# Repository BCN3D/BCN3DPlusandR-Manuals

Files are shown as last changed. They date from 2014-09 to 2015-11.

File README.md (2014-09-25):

BCN3D+ Manuals
==============

Close up view of the printer

We've made some pretty awesome manuals to help you assembling the BCN3D+. We have two versions, the **PDF** and the **3DVIA**. All the manuals are based on the 3D model of the printer, so you'll be able to see 3D assemblies with all the parts and pieces.

Again, the manuals are supposed to guide you in the process of assembling the printer. If you detect any mistake or improvement, please let us know by submitting and Issue in the git repo.

The good stuff comes when you use the 3DVIA manuals. An executable application lets you rotate, zoom and select the parts in a 3D dimensional way. Easy as pie!

3DVIA visualization example

You can find the following assembly manuals:

+ BCN3D+ 3D printer
+ BCNozzle, the full metal hot-end upgrade for multiple 3D printers
+ Dual Extruder, all the steps to assembly the dual extruder upgrade

*New and updated Manuals are coming... just follow us on Github to be up to date!*

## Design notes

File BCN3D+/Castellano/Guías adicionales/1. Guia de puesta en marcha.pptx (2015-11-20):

## Puesta en marcha Encendido y ajustes previos al funcionamiento de la máquina

Equipo RepRapBCN

## Puesta en marcha

- Con el conexionado listo y el firmware ya instalado se puede arrancar la máquina. Para hacerlo sólo hay que apretar el interruptor de la parte posterior.
- La pantalla debería quedar como en la imagen:
- Cuando se haga por primera vez es importante estar atentos a posibles ruidos o cualquier anomalía.
NOTA:

Si ha recibido su maquina ya montada no es imprescindible que realice muchas de las siguientes comprobaciones aunque es recomendable hacerlas para detectar posibles problemas y para familiarizarse con su funcionamiento.

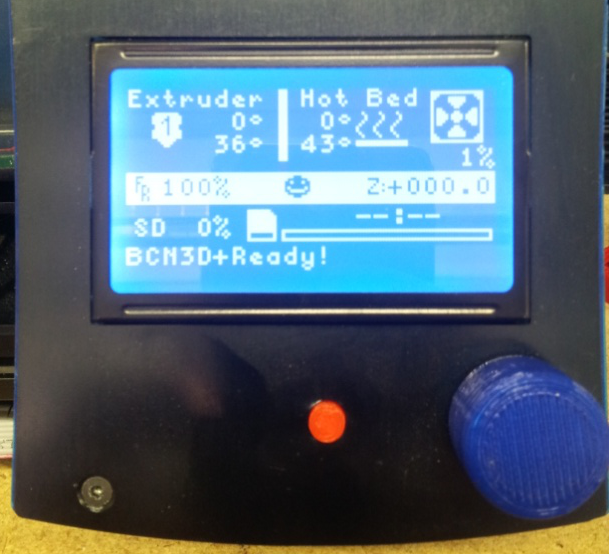
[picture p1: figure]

Dudas?

## Puesta en marcha

Árbol de menús de la pantalla

- Para entrar en el árbol pulse el botón giratorio:
- Prepare
  - Dissable steppers (desbloquea motores para movimiento manual)
  - AutoHome (Lleva la máquina a x=0, y=0, z=0)
  - Preheat (Precalentamiento de máquina)
  - Cooldown (Enfriamiento de máquina)
  - Move Axis (Movimiento de ejes desde pantalla)
- Control
  - Temperature
    - Nozzle (elección manual de temperatura del extrusor)
    - Bed (elección manual de la temperatura de la base calefactora)
  - Motion

Para saber mas sobre el resto de opciones del menú visitad y comentad nuestro foro. (http://www.reprapbcn.com/es/forum)

Dudas?

## Puesta en marcha

- Comprobaciones de funcionamiento: Termistores y motores X e Y

- Termistores:
  - Verificar que la temperatura que miden es “lógica”. La pantalla debería mostrar temperaturas que ronden la temperatura del ambiente.
- ~025/000°
- Orientación de motores X e Y:
  - Entrar en el menú: Prepare > Move Axis
  - Seleccionar 1mm y seleccionar X. Al girar la rueda en sentido horario el carro con el extrusor debería moverse hacia la derecha (acercarse al final de carrera).
  - Si no lo hace, apagar la máquina y cambiar orientación del conector del motor X en la placa.
  - Hacer esta misma comprobación para el eje Y. (en este caso debe alejarse del final de carrera Y)

Dudas?

## Puesta en marcha

- Comprobaciones de funcionamiento : Motor Z

- Orientación del motor Z:
  - Seleccionar Z en el menú Move Axis
  - Girar la rueda MUY POCO en sentido horario
  - Comprobar que los dos motores giran en el mismo sentido.
  - Si no es así parar máquina y girar una de las dos conexiones. (Ambos motores deberán seguir el mismo código de colores)
  - Volver a mover el eje. Ahora se puede girar la rueda sin miedo.
  - Comprobar que el eje Z está subiendo al girar la rueda en sentido horario.
  - Si no lo hace girar los dos conectores

Dudas?

## Puesta en marcha

- Sistema de ejes

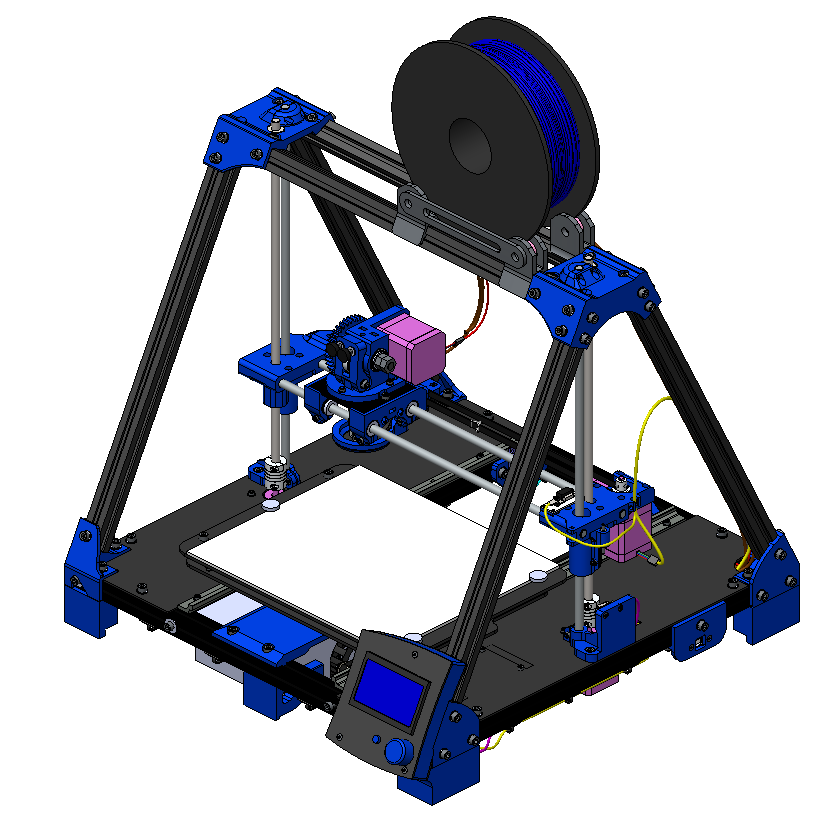
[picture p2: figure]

EJE X

EJE Y

EJE Z

EJE E

Dudas?

## Puesta en marcha

Comprobaciones de funcionamiento: Finales de carrera

- Localizar todos los finales de carrera (X, Y y Z en este orden)
- Comprobar que los finales de carrera contactan correctamente con la parte móvil correspondiente de cada eje en cuanto ésta se acerque a ellos y que el LED se enciende cuando los pulsa.
- Si al pulsar un final de carrera se corta la alimentación de la máquina es probable que alguno de los extremos del final de carrera esté conectado en sentido incorrecto.

Para el eje Z realizar estas comprobaciones con el prisionero de regulación en la posición más alta (que el tornillo salga lo máximo por debajo de la pieza) para evitar contacto entre extrusor y base.

Dudas?

## Puesta en marcha

A continuación se va a comprobar el funcionamiento de los finales de carrera manualmente:
  - Acceder al menú prepare y colocar el cursor en la opción Autohome SIN PULSARLA
  - En el momento en que se active el Autohome el eje X irá hacia el final de carrera, luego lo hará el Y, y luego el Z.
  - A medida que los ejes se muevan, pulsar con la mano el final de carrera correspondiente. Si al pulsar alguno de los finales de carrera no se detiene el movimiento del eje, parar máquina de inmediato.
  - Si se produce este error querrá decir que, aunque están bien conectados, las posiciones de los finales de carrera en la placa están intercambiadas. Comprobarlo y conectarlo correctamente.
  - Cuando la prueba anterior se realice correctamente, pulsar Autohome otra vez para verificar el contacto de la pieza móvil con el final de carrera.

El objetivo es activar los finales de carrera con el dedo antes de que lo hagan las partes móviles de la máquina

Dudas?

## Puesta en marcha

- Comprobaciones de funcionamiento: Resistencias y calentamiento

- Activación del calentamiento:
- Seleccionar en el menú prepare > Preheat PLA.
- Al escoger esta opción se empezará a calentar la base y el extrusor hasta las temperaturas establecidas en el firmware.
- Comprobar que en la pantalla principal aparecen temperaturas objetivo: Extrusor y Base calefactada.
- Dejar calentar y ver si se llega a la temperatura objetivo. (El extrusor debe tardar menos de 5 min, mientras que la base puede llegar a tardar 15 min).

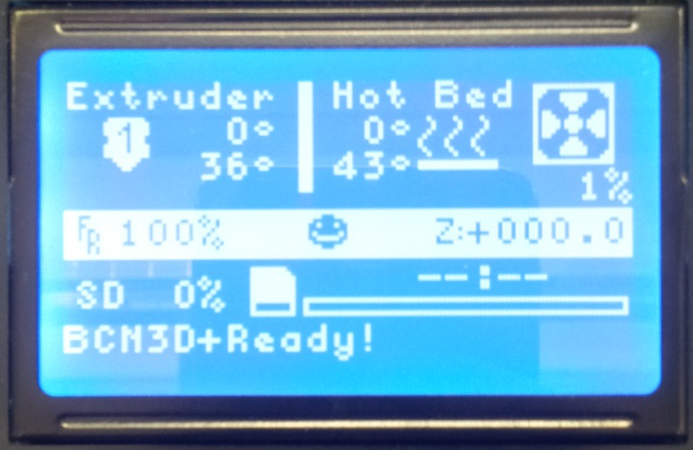
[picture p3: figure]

Dudas?

## Puesta en marcha

Comprobaciones de funcionamiento: Extrusor

- Una vez el extrusor esté a la temperatura preestablecida para el PLA, pulsar 1mm > Extruder en el menú de Move Axis y comprobar que el engranaje grande gira en el sentido de las agujas del reloj.
- Si no es así, cambiar la orientación del conector del motor en la placa electrónica.

Esta comprobación se deber realizar con la máquina caliente y el extrusor a la temperatura del hilo que se va a extruir (PLA ± 190/220ºC , ABS ± 230/250ºC)
Para modificar las temperaturas objetivo seleccionar Temperature >Nozzle en el menú Control

Dudas?

## Puesta en marcha

Comprobaciones de funcionamiento: Extrusor

- Cuando el sentido de giro ya sea el correcto, comprobar que el ventilador del disipador (el mas pequeño esté funcionando)
- Abrir el fijador del extrusor y pasar hilo por el agujero. Asegurarse que el hilo encara el segundo agujero
- Introduciendo hilo con suavidad hasta que éste empieza a salir fundido por la boquilla.
- Cerrar el fijador de manera que ejerza una cierta presión.
  - Demasiada fuerza erosionará el hilo y no traccionará correctamente con la parte grafilada
  - Poca fuerza dejará el hilo suelto y tampoco saldrá.

Esta comprobación se deber realizar con la máquina caliente y el extrusor a la temperatura del hilo que se va a extruir (PLA ± 190/220ºC , ABS ± 230/250ºC)
Para modificar las temperaturas objetivo seleccionar Temperature >Nozzle en el menú Control

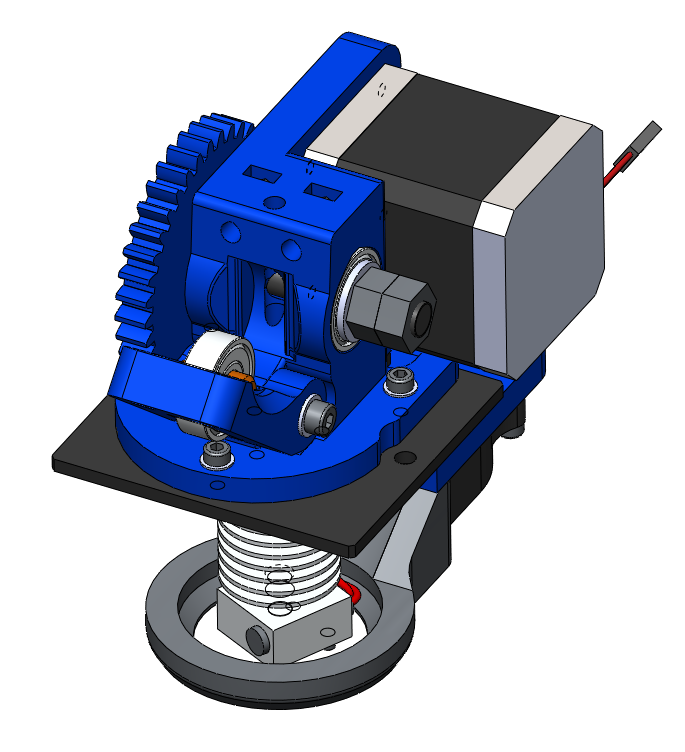
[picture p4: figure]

Dudas?

## Puesta en marcha

Comprobaciones de funcionamiento: Extrusor

- Una vez preparado el hilo se accede al menu prepare > move axis > 1mm > Extruder SIN apretarlo.
- Colocar los dedos en la parte del hilo que justo entra por el orificio superior y le damos a Extrude
- Comprobar si el extrusor tira el hilo (dejando que este entre. NUNCA intentando evitar el movimiento del hilo)
- Pulsar varias veces a Extrude hasta que el plástico salga de manera fluida y continua por la boquilla.

Vigilar no poner los dedos en contacto con ninguna parte móvil que no sea el hilo!

Dudas?

## Esperamos que hayais disfrutado de la experiencia! No olvidéis seguirnos en Twitter y Facebook Para cualquier duda visita nuestro foro (http://www.reprapbcn.com/es/forum)!

- Equipo RepRapBCN

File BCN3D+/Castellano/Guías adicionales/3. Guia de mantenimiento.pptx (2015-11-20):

## Recomendaciones de uso y mantenimiento Algunos consejos para que pueda sacar el máximo partido a su impresora y asegurar su buen funcionamiento

Equipo RepRapBCN

## Recomendaciones de uso y mantenimiento

- Ajustes del eje Z

- A pesar de tener la máquina calibrada, es posible que al empezar a imprimir la pieza, la boquilla quede demasiado alta. Esto se identifica porqué en vez de dejar un hilo constante, va soltando gotitas de material fundido.
- Se puede solucionar provisionalmente este problema girando a mano las dos varillas del eje Z en sentido antihorario. Hay que vigilar de girar el mismo número de pasos las dos varillas para no descalibrar la máquina.

Las gotitas también se producen cuando el extrusor aun no ha llegado a estabilizarse en fundir plástico. Esperar unas cuantas pasadas antes de diagnosticar el problema.

Tener mucho cuidado, ya que son elementos móviles accionados por el motor!

Dudas?

## Recomendaciones de uso y mantenimiento

- Extracción de piezas

- Para retirar las piezas de la base, retirar primero el vidrio quitando al menos uno de los tornillos blancos (de poliamida) que lo sujetan.
- Una vez extraído de la máquina, separar las piezas de la base. De esta manera se reduce considerablemente el riesgo de descalibrado de la máquina.
- Cada cierto número de impresiones es recomendable limpiar la base.

Dudas?

## Recomendaciones de uso y mantenimiento

- Adherencia de la superficie caliente

- Para mejorar la adherencia de las piezas a la base calefactada es bueno usar laca (suministrada en el kit) especialmente para el ABS.
- Para aplicar la laca sobre el vidrio vaporizarla a una distancia entre 30 y 40 cm. Sobre toda la superficie del vidrio.

Dudas?

## Recomendaciones de uso y mantenimiento

Limpieza del extrusor

- Cada cierto tiempo de uso, es recomendable limpiar el exterior de la boquilla del extrusor.
- Se puede hacer dando varias pasadas por la boquilla (con el extrusor caliente) con un paño mojado en acetona (o producto similar).

El contacto con el extrusor puede producir quemaduras graves. Tener mucho cuidado al realizar este paso. Igualmente, no mantener el contacto entre el paño y la boquilla muchos segundos, ya que se puede quemar paño.

Dudas?

## Recomendaciones de uso y mantenimiento

- ¿Cuándo calibrar?

- Cuando se aprecie una diferencia de altura de la primera capa al empezar una impresión.
- Cada cierto tiempo y según el gusto personal.
- Lo importante es que la máquina imprima la primera capa bien, con el material bien pegado a la superficie.

Dudas?

## Esperamos que hayais disfrutado de la experiencia! No olvidéis seguirnos en Twitter y Facebook Para cualquier duda visita nuestro foro (http://www.reprapbcn.com/es/forum)!

- Equipo RepRapBCN

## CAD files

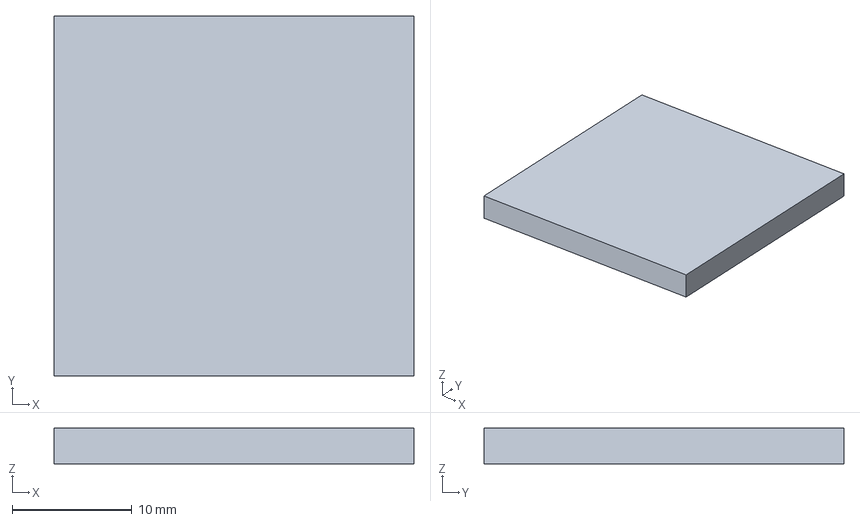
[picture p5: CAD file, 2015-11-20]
Dual Extruder/Calibration, set up/Calib.amf
30.0 x 30.0 x 3.00 mm

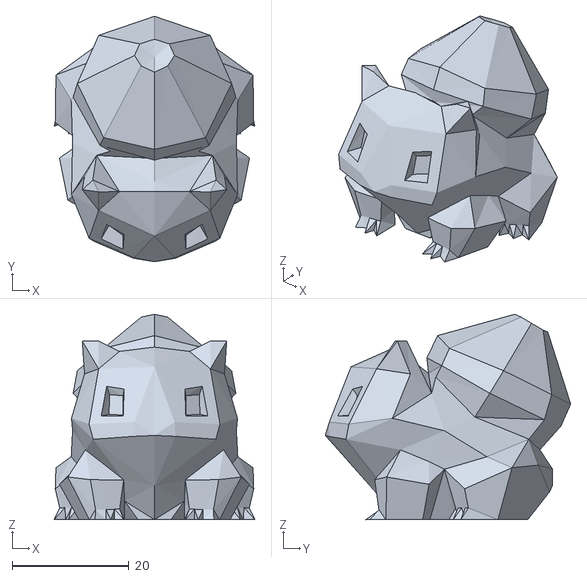
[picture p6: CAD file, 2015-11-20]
Paste extruder/Files for the set up, first run/STLs/bulbasaur.STL
34.4 x 42.0 x 35.2

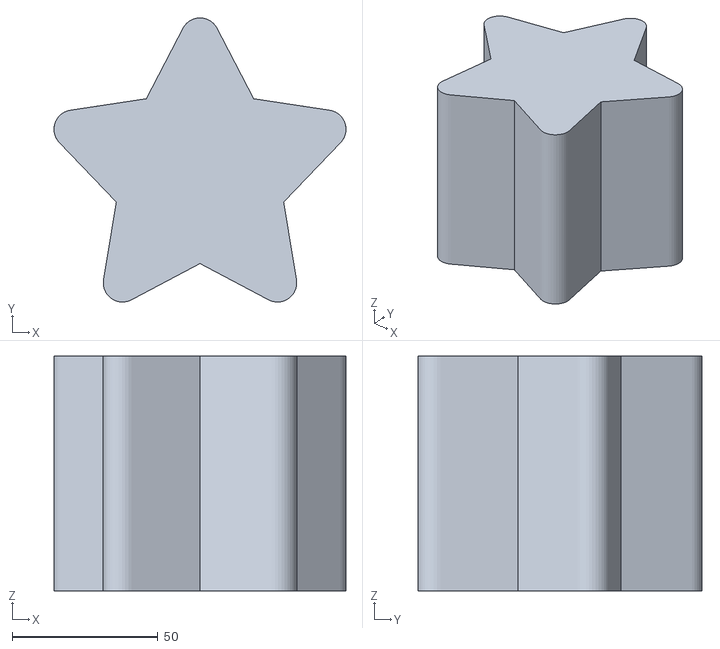
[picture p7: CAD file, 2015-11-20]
Paste extruder/Files for the set up, first run/STLs/star.stl
100.3 x 97.6 x 80.5

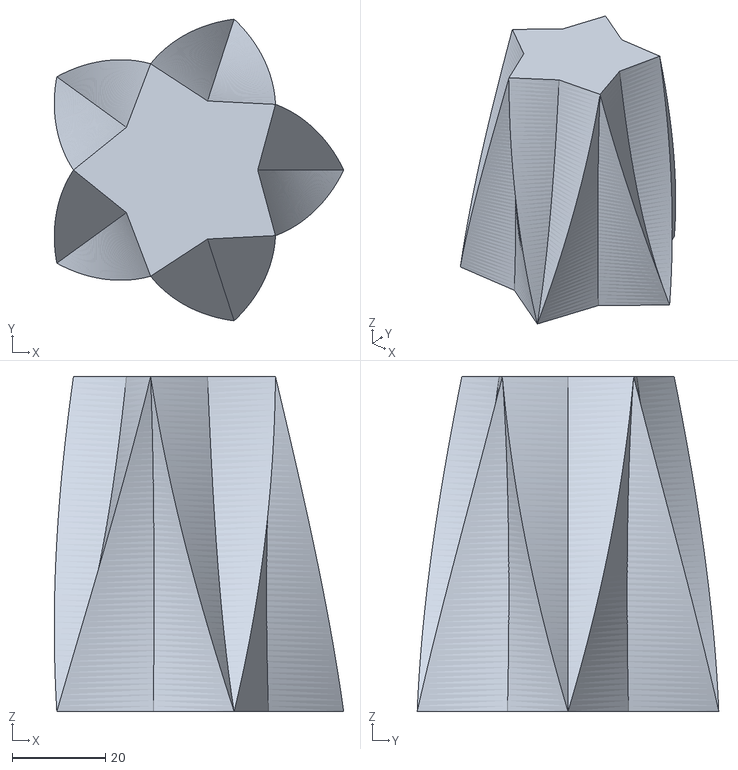
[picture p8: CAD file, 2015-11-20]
Paste extruder/Files for the set up, first run/STLs/star-vase.stl
62.2 x 64.8 x 72.0

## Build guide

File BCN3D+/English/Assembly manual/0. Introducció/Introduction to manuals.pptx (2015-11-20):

## Introduction to manuals Information for the proper use of the manuals

- RepRapBCN Team

## Welcome

- If you're holding this book means you're ready to start assembling your BCN3D+ . We hope you will enjoy the experience during the construction process of your printer and also after creating your pieces.
- Before you start we going to make a brief introduction to the series of manuals for a even easier experience.

## Location of the manuals

- In the directory of manuals from the SD card are 8 folders. Each corresponds to a subsystem of the printer and will assemble them in the indicated order.
- This way we begin with the structure of the printer, to continue with the elements that allow movement in all three axes (Y, X and Z). With all the mechanics prepared just miss to add the electronics and LCD screen, and finally the wiring.

## File types

- In each folder you will find 2 types of file with the same name:
  - *.exe file is an application that offers an interactive guide assembly. You can zoom, move and rotate the view. We recommend this to use because it allows much better understanding of the assembly.
  - *.pdf file is a sequence of images that correspond to the interactive slides manual. It's equivalent to the above but designed for those users who can not run the application (especially Mac and Linux). Also useful is the .pdf file if you want to assemble the printer with a paper edition of the manual.

## Interactive operation manual

- The application of the interactive manual is easy to use, you just need to know the icons to manipulate the views of the 3D printer assembly :

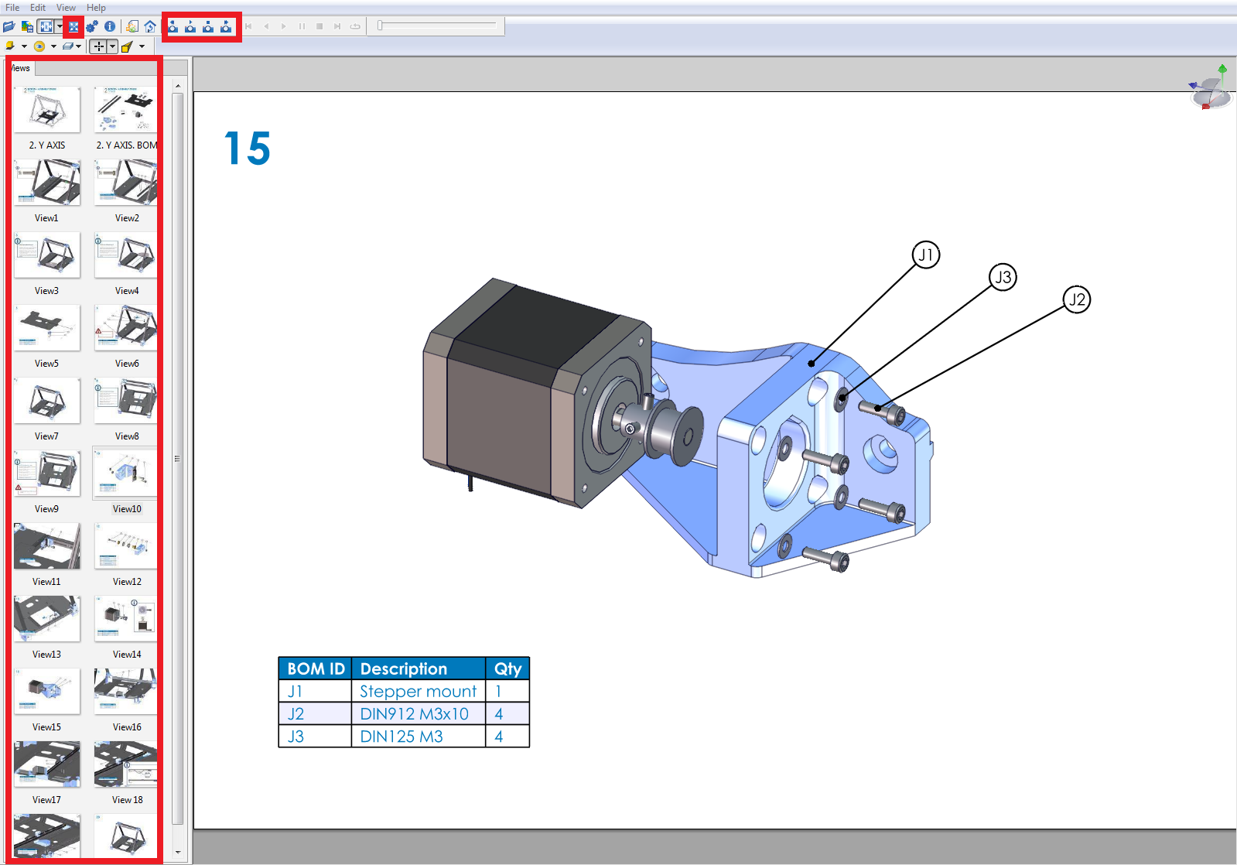
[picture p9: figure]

## Interactive operation manual: Navigation

  - Sequential Navigation: To get around the manual you can use the buttons on the top. With them you can go back to a slide, play in auto mode, stop the auto play and go to a slide, in the order they appear.
          - Sequential Navigation: To get around the manual you can use the buttons on the top. With them you can go back to a slide, advance in auto mode, stop the auto play and go to a slide, in the order they appear.

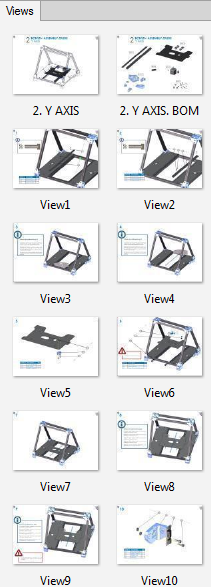
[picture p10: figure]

## Interactive operation manual: Navigation

- Zoom in / out: By rotating the mouse wheel you can change the zoom and focus on the area you want.
- Move: With the same wheel, but using it in button mode you can scroll the image. This way you can move to different parts of the printer without changing the perspective.
- Rotate: If you need to get another point of view, you can change the perspective by using the right mouse button, holding it down while you rotate the view.

## Structure of the chapters

1st Page: Presentation of Chapter
The title of the chapter and the whole machine is displayed on the first slide, with the silhouette of the pieces you have assembled so far and in color which have to be installed in this chapter.

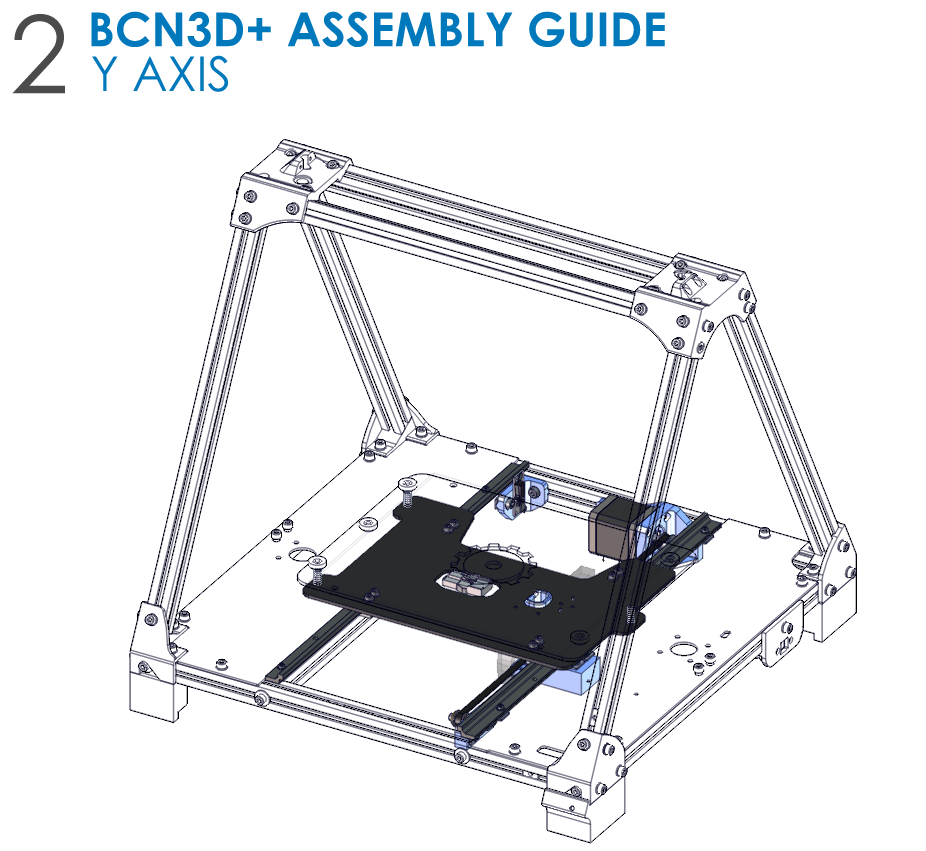
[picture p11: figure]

## Structure of the chapters

2nd page: parts distribution in boxes
The second page is a summary of the parts to be used in this chapter, grouped by type of part, to identify where you have to look for each one.
It is important to remember that NOT all parts are listed only the main ones, is just to know in which boxes are the necessary equipment.

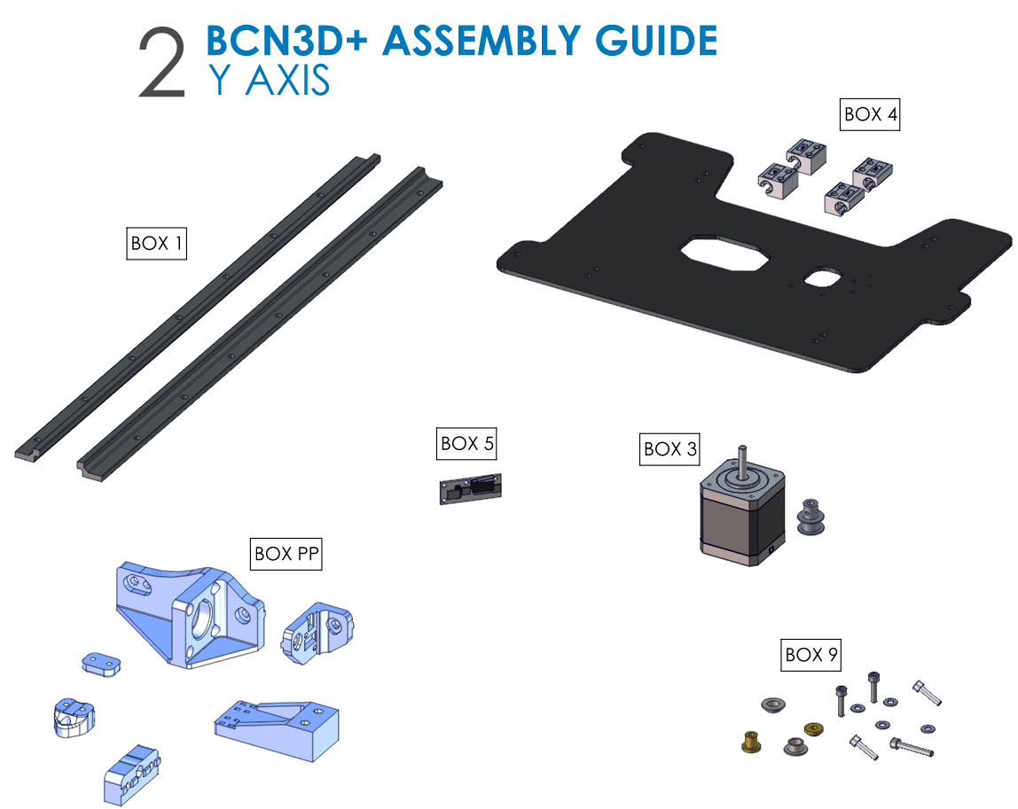
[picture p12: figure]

## Structure of the chapters

Other pages: Installation steps
Each of the steps shown in a slide type that has common elements: slide number, steps to follow, list of components, callouts and annotations component ID number (only when necessary).

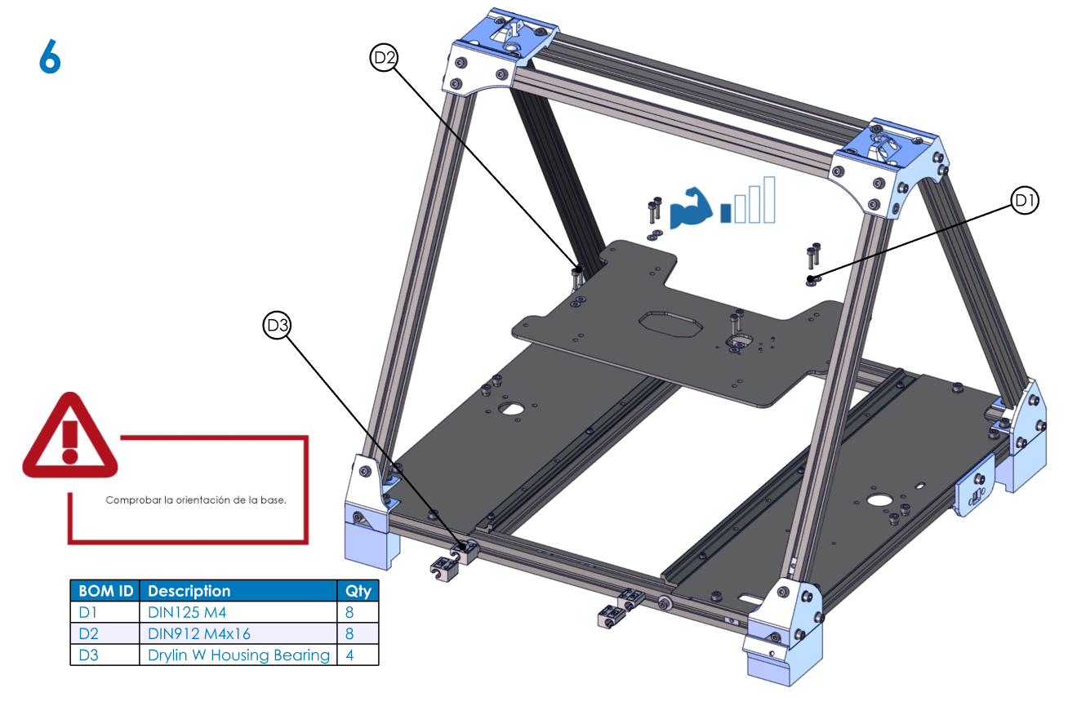
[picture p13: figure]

## Structure of the chapters

- Common elements
- Slide Number: Located in the top left, and helps identify the step that is being processing.
- Steps to perform: Figure of the machine tells you the components to be mounted on that step. When you change the slide, the components are moved to the mounting position. Back and forth you can get a better idea of how to mount the component, and you can repeat this step as many times as you needed.

## Structure of the chapters

- Common elements
- List of components: The table is usually found on the bottom left (although sometimes may appear elsewhere) indicates the components that you need in that step. The first column is the ID part of the manual, the second is the name and the third the quantity. We recommend to prepare all the parts of the table before you start assembling the step.
- The callouts component indicator: Indicator used to easily identify the parts to be assembled in 3D view. The callouts still appears even rotate the 3D view and if necessary, you can move to have a clearer view and to avoid crossing the image. Just click on the callouts itself and without releasing the mouse button, drag it to the desired position.

## Structure of the chapters

- Notes: In the slides that require it, a series of annotations. Each symbol corresponds to the message that is described below:

INFORMATION: Always accompanied by an explanatory note that is not essential for the assembly of the printer but is useful to facilitate understanding of the manual.

CAUTION: This icon is always accompanied by an essential explanatory annotation for the correct assembly of the printer.

NOT: Indicates something that should not be as in the picture. It also used to help distinguish between components to be used.

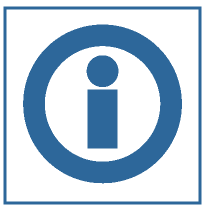
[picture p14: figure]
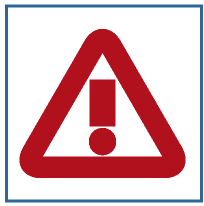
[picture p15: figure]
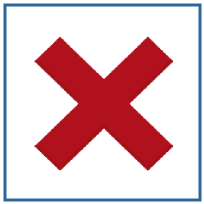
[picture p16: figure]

## Structure of the chapters

TIGHTEN WITH FINGER: Indicates something that should hold it by hand until it locks in a definitive way.

THREAD: Indicates the component that affects must be threaded.

FLAT SURFACE: Indicates that the operation referred to must be performed on a flat surface. Affects critical parts of the structure and serves to ensure a good reference planes for other mechanisms.

FLANGE CLOSE: This icon indicates that the corresponding step needs to close one or more flanges at the indicated position.

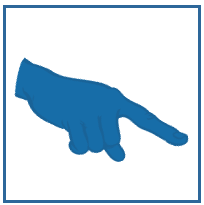
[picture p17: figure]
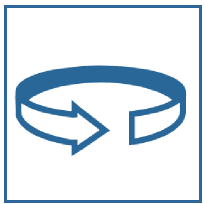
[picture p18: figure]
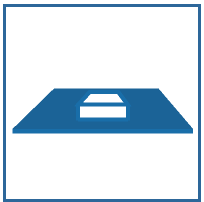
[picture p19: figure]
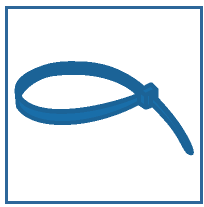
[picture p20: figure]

## Structure of the chapters

SOFT TIGHTEN: Indicates that this torque should be smooth, simply to ensure that the screw is attached to the component without deforming. It usually affects plastic components that can break under excessive force.

TIGHTEN STRONG: Indicates that this torque must be strong to ensure that the component is properly fixed. It usually affects metallic components that transmit important efforts under operation.

FLAT SURFACE: Indicates that the operation referred to must be performed on a flat surface. Affects critical parts of the structure and serves to ensure a good reference planes for the mechanisms.

TAPE: Indicates to use adhesive (or similar) tape during the step to temporarily hold some component.

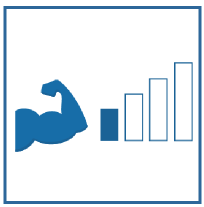
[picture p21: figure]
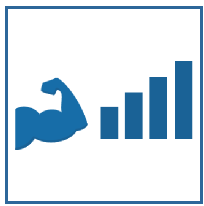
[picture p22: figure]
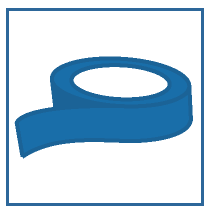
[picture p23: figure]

## Structure of the chapters

Last Page: End of Chapter
The last page of each chapter shows the final step of the assembly procedure.

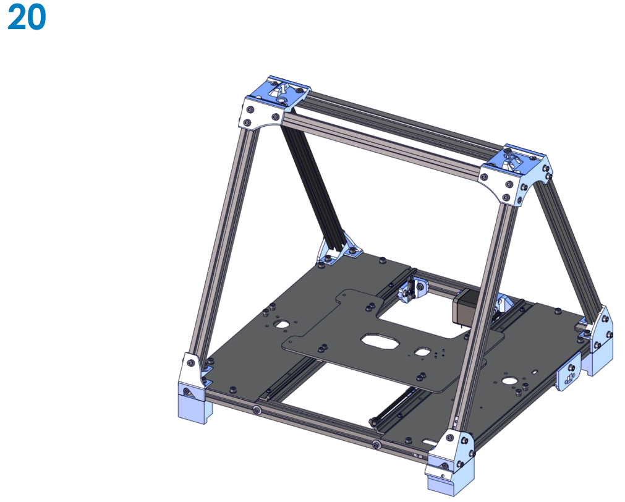
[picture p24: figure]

## We hope you enjoy the experience! Do not forget to follow us on Twitter and Facebook For any questions visit our forum!

- RepRapBCN Team

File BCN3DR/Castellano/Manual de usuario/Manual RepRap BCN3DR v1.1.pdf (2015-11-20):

User Manual | RepRapBCN

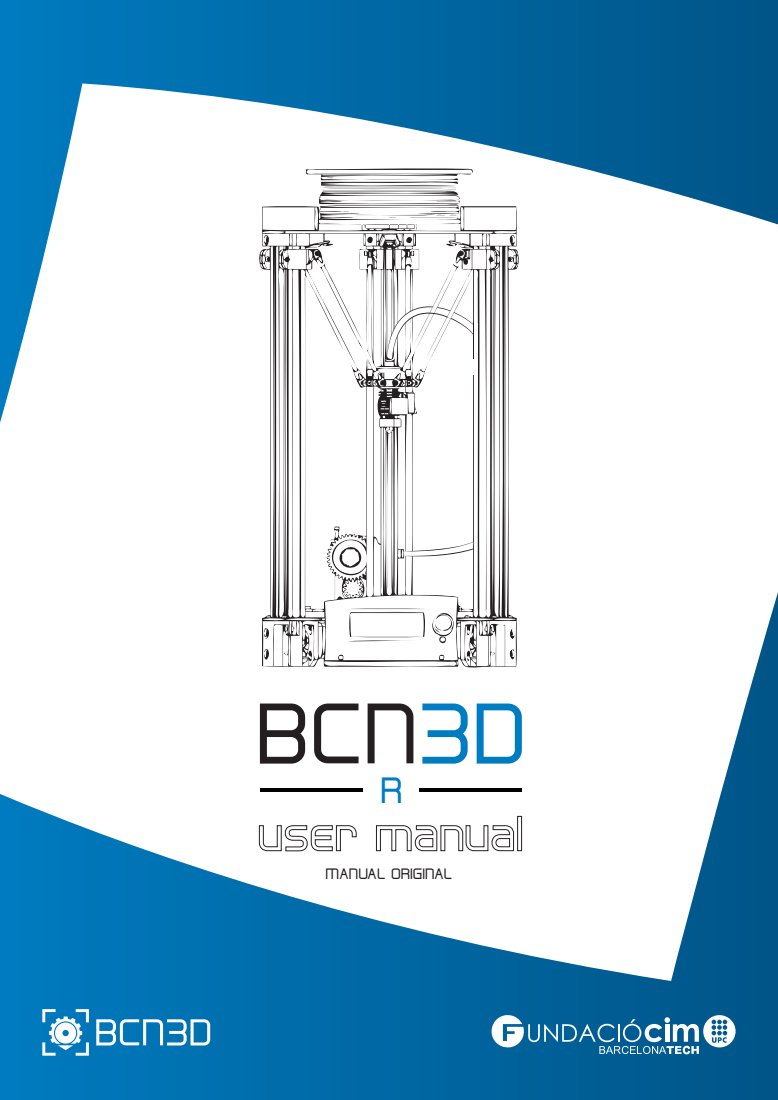
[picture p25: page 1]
MANUAL ORIGINAL

### 1. INFORMACIÓN PREVIA

Especificaciones
Tecnología FFF
Conformidad
Seguridad

### 2. PUESTA EN MARCHA

Herramientas y accesorios
Diagrama de la BCN3DR

### 3. PRIMER CONTACTO

Calibración
Carga de filamento
Trabajando con la BCN3DR

### 4. CONTROL LCD

Pantalla principal
Pantalla de menú

### 5. ARCHIVOS STL

Obtención de archivos STL
Edición y reparación del STL Interfaz de Netfabb
Reparación
Orientar y mover a origen
Generación del G-CODE
Configuración del Slic3r
Uso básico del Slic3r
Transferencia del Gcode a la BCN3DR

### 6. IMPRESIÓN DESDE TARJETA SD Y USB 7. FILAMENTOS

PLA

### 8. FIRMWARE

¿Qué es el firmware y cuándo actualizarlo? ¿Cuándo es necesario actualizar el firmware? Descargar el IDE de Arduino

### 9. SOLUCIÓN DE PROBLEMAS 10. DIAGNÓSTICO DE LA CALIDAD DE IMPRESIÓN 11. MANTENIMIENTO 12. CONSEJOS Y ADVERTENCIAS 13. ASISTENCIA TÉCNICA RepRapBCN 14. GLOSARIO 15. GARANTÍA , DEVOLUCIONES Y POLÍTICA DE SUSTITUCIÓN 16. TÉRMINOS Y CONDICIONES DE SERVICIO

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
# INDICE

Material Extrusion Fused Filament Fabrication (FFF) Ø370 mm x 560 mm
7kg (sin bobina de filamento)

Diámetro: 170mm
Altura: 180mm

1

0,1-0,35mm (con boquilla estándar de 0,4mm) 0,2-0,5mm (con boquilla de 0,6mm)

Eje x y z: 0,05mm

15-35ºC
260ºC
3mm

PLA

Arduino Mega 2560 + RAMPS 1.4

Targeta SD (funcionamiento autónomo) Cable USB (control mediante Repetier Host)

Específico BCN3DR (basado en Marlin) STL
Slic3r, Cura
AC 100–240 V, ~0.2-0.4 amps, 50–60 Hz 60W

### 1. INFORMACIÓN PREVIA

### Especificaciones

Tecnología de fabricación: Dimensiones generales:
Peso:

Volumen de impresión:

Número de extrusores:

Altura de capa:

Resolución de posicionado:

Temperatura funcionamiento: Temperatura de extrusor máx.: Diámetro de filamento:

Materiales admisibles:

Electrónica:

Conectividad:

Firmware:
Archivos compatibles:
Software preparación archivos: Alimentación eléctrica:
Consumo eléctrico:

### Tecnología FFF

La BCN3DR es una impresora 3D basada en la tecnología FFF (por sus siglas en inglés, Fused Filament Fabrication).

Esta tecnología permite fabricar piezas por medio de la deposición de material fundido.Para ello, se parte de un modelo digital que se secciona en capas finas. El cabezal realiza los movimientos para depositar el material de una capa, luego realiza un pequeño desplazamiento vertical y continua con la siguiente capa. El proceso se repite hasta realizar

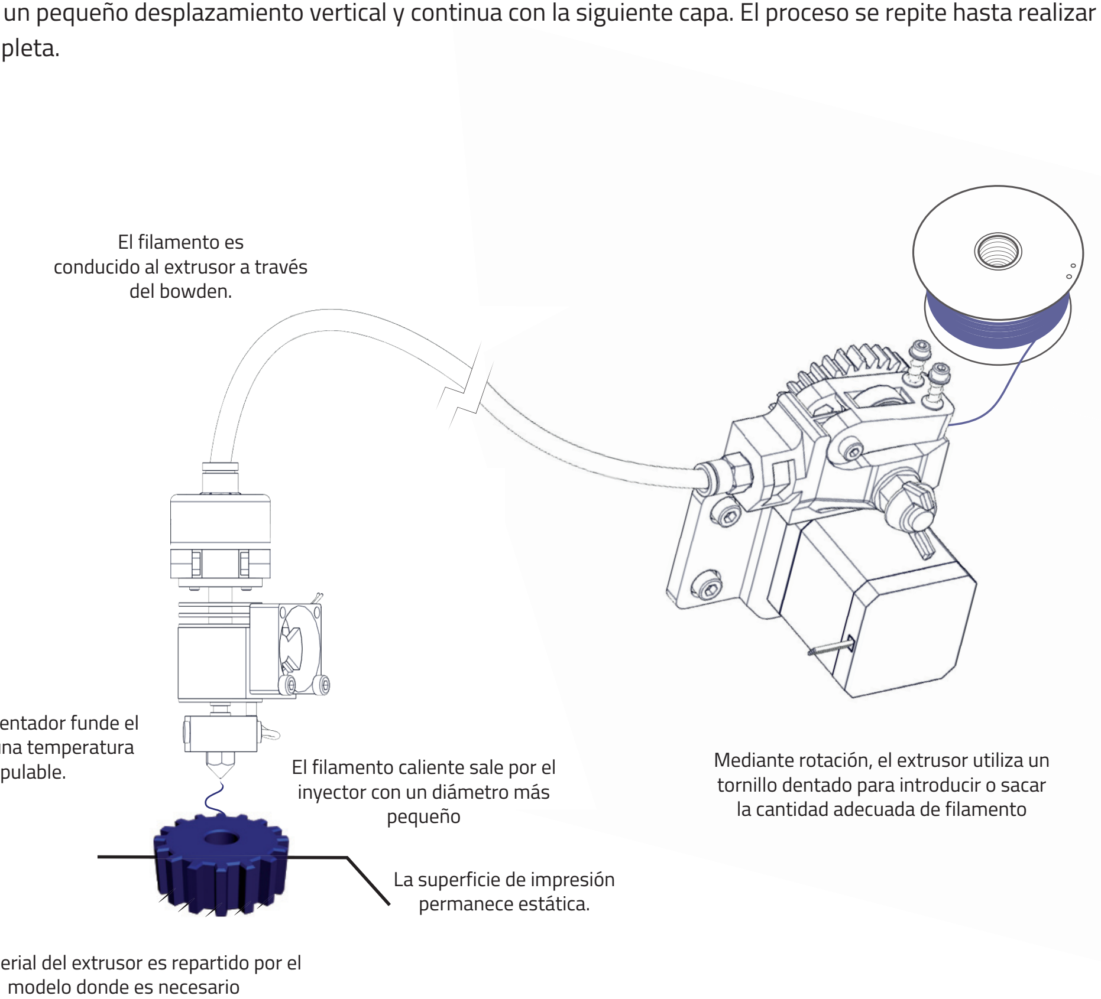
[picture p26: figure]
la cantidad adecuada de filamento; El filamento es conducido al extrusor a través del bowden.; La superficie de impresión permanece estática.; modelo donde es necesario; El filamento caliente sale por el inyector con un diámetro más pequeño

la figura completa.

Mediante rotación, el extrusor utiliza un tornillo dentado para introducir o sacar

Un bloque calentador funde el filamento a una temperatura manipulable.

El material del extrusor es repartido por el

### Conformidad

Por medio de la presente Fundació Privada Centre Cim declara que BCN3DR cumple con los requisitos esenciales y cualesquiera otras disposiciones aplicables o exigibles de las Directivas.

Directiva de Baja Tensión 2006/95/CE Directiva de máquinas 2006/42/CE Directiva RoHS2011/65/UE

### Seguridad

Para evitar posibles riesgos residuales para el usuario, se ruega leer con atenciónlas siguientes medidas de seguridad.

REPRAPBCN SE EXIME DE CUALQUIER RESPONSABILIDAD SI EL USUARIO NO RESPETA LAS SIGUIENTES INDICACIONES DE USO:

- Muy importante. Como cualquier electrodoméstico, no tocar los bornes de los cables provenientes de la red eléctrica. La tensión es 230V y existe el riesgo de electrocución. Los demás cables de la máquina trabajan a 12V y no existe riesgo alguno.
- Esta máquina genera y emite radiofrecuencias durante su uso. Es importante instalar y hacer uso del equipo de acuerdo a las instrucciones de este manual para evitar interferencias perjudiciales con electrodomésticos como la televisión o la radio. En caso de que la máquina cause interferencias, aumente la separación entre ésta y los otros electrodomésticos.
- Los materiales de impresión no son inocuos y pueden emitir humos tóxicos. Imprimir siempre en lugares abiertos o con ventilación.
- No respirar a menos de 25cm del cabezal o cabezales extrusores en funcionamiento.
- No situar ningún objeto ni ninguna parte del cuerpo entre las partes móviles de la máquina cuando esté encendida.
- No tocar las partes calientes (hotend) cuando la máquina esté encendida, ni durante los 15 minutos posteriores a su funcionamiento.
- No conectar o desconectar ningún dispositivo y/o conector eléctrico con la máquina conectada a la corriente.
- Supervisar el buen funcionamiento de la impresora durante su funcionamiento
- En caso de emergencia, detener la máquina mediante el botón de bloqueo y desconectar la alimentación eléctrica.

Para remarcar la importancia de la seguridad, se han indicado los riesgos mediante etiquetas indicativas, dispuestas en la máquina en las zonas pertinentes.

Señalización de seguridad
Las siguientes señales se han puesto en la impresora para prevenir a los usuarios sobre las áreas de riesgo que pueden entrañar las partes de la máquina o de posibles acciones que no son recomendables para el buen funcionamiento de la impresora 3D.

Superfície caliente dejar enfriar antes de manipular.

Partes móviles peligro de aplastamiento desconectar antes de manipular.

### 2. PUESTA EN MARCHA

### Contenido de la caja

El kit de la BCN3DR se entrega dentro de una caja de cartón debidamente asegurada, de medidas 600 mm largo, 400 mm ancho y 250 mm alto.

Piezas impresas:

- Chapas metálicas cortadas
- Varillas y guías
- Motores NEMA 17
- Arduino Mega , Ramps 1.4, LCD y drivers Pololus
- Cableado
- Ventiladores
- Tornillería , rodamientos i correas
- Tubo Bowden y BCNozzle
- Vidrio de la superficie de impresión
- Tarjeta SD para cargar nuestros archivos a la impresora
- Cable alimentación
- Transformador alimentación
- Bobina 1Kg PLA
- Laca (3DLAC)
- Herramientas

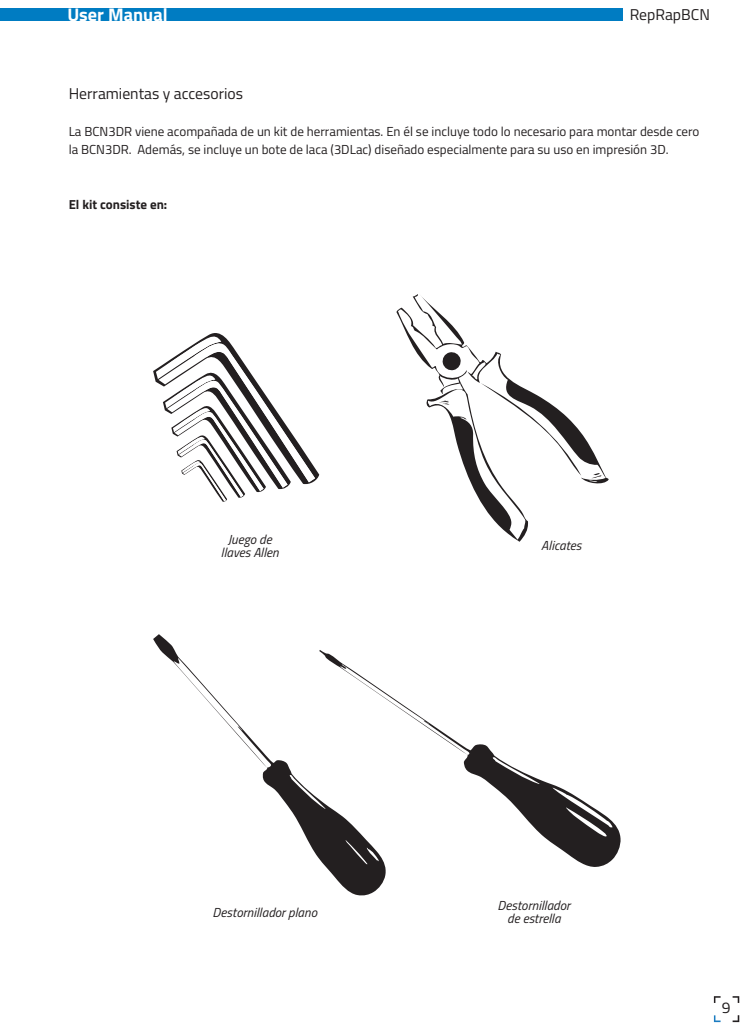
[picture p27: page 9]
Herramientas y accesorios; Juego de llaves Allen; Destornillador plano; Destornillador; de estrella; Alicates

La BCN3DR viene acompañada de un kit de herramientas. En él se incluye todo lo necesario para montar desde cero
la BCN3DR. Además, se incluye un bote de laca (3DLac) diseñado especialmente para su uso en impresión 3D.

El kit consiste en:

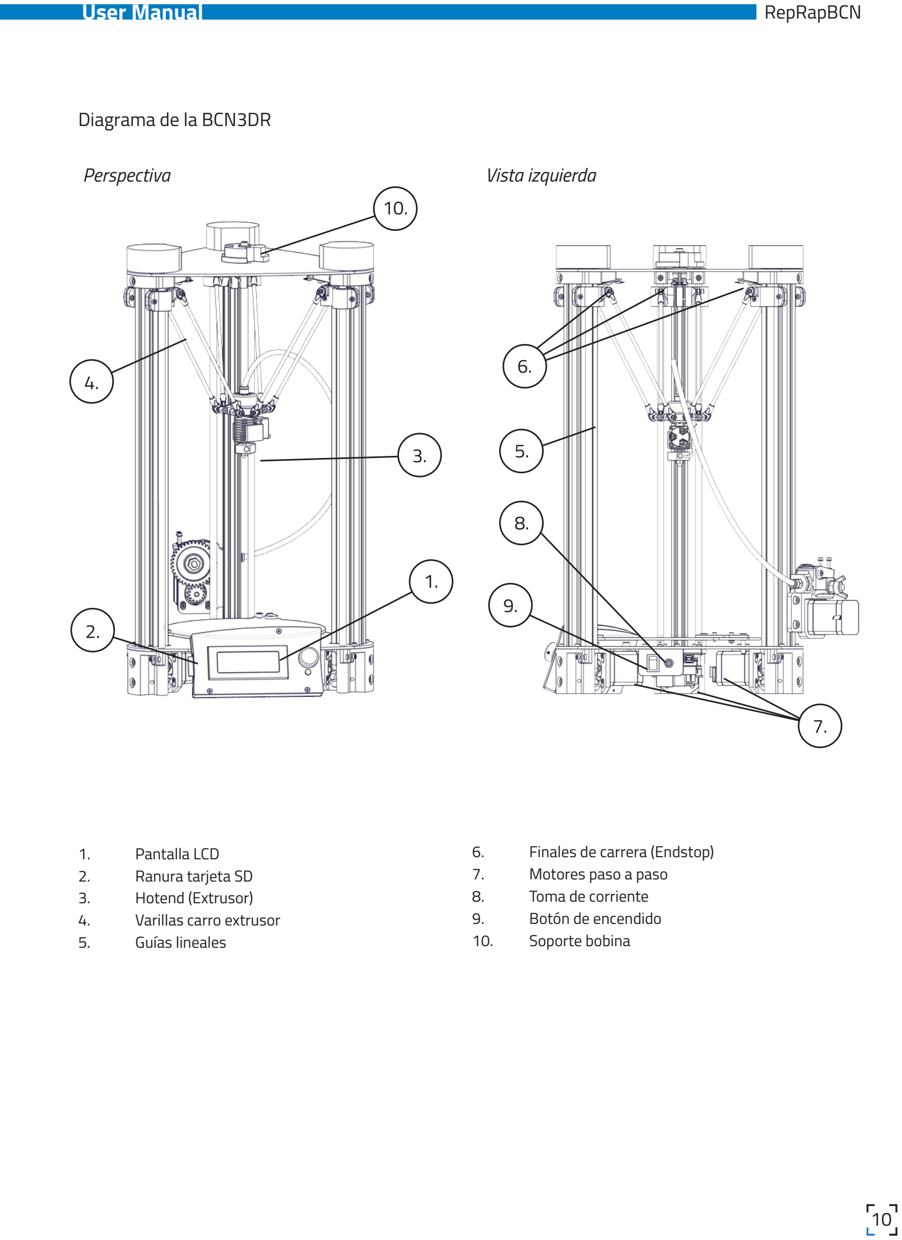
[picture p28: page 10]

6. Finales de carrera (Endstop)
7. Motores paso a paso
8. Toma de corriente
9. Botón de encendido
10. Soporte bobina

### Diagrama de la BCN3DR

1. Pantalla LCD
2. Ranura tarjeta SD
3. Hotend (Extrusor)
4. Varillas carro extrusor
5. Guías lineales

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
Perspectiva | Vista izquierda

Hotend

1. Disipador de calor
2. Barrera térmica
3. Bloque calefactor
4. Boquilla (Nozzle)
5. Ventilador Hotend

Extrusor

6. Balancín
7. Tornillo de apriete
8. Bowden
9. Pneufit

Electrónica

10. Pololus
11. Arduino + RAMPS
12. Conector USB

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
### 3. PRIMER CONTACTO

### Calibración de la altura de la superfície de impresión

Para un correcto funcionamiento, es clave que el plano de movimiento de la boquilla sea perfectamente paralelo a la superficie de impresión.

Y para conseguirlo es necesario calibrar la orientación de la superfície de impresión mediante los 3 tornillos de que dispone.

Con una base mal calibrada NO SE PUEDE IMPRIMIR, y se corre el riesgo que la boquilla (nozzle) choque contra el cristal de la superfície de impresión, o que la primera capa de la impresión no se adhiera bien. Para calibrarla correctamente se deben seguir los siguientes pasos:

1. Hacer Autohome (Prepare > Autohome) para que la máquina mueva los ejes a la posición inicial.
2. Apretar los tres tornillos de la superficie de impresión M5 ( los más grandes ) hasta comprimir los muelles que sujetan la base para bajar la superficie de impresión.
3. Aflojar los mismo tornillos 5 vueltas. Así evitaremos que el nozzle golpe con el vidrio en el siguiente paso.
3. En el menú de la maquina: Prepare > Move axis > 10mm > Move Z desplazaremos la plataforma del extrusor a Z: +000.00 mm.
4. Después desplazaremos el nozzle en el plano del cristal hacia los tornillos de sujeción, para ello iremos a : Prepare > Move axis > 1mm > Move X y lo desplazaremos a X: -085.0mm.
5. Aflojar el tornillo anteriormente apretados M5 ( el más grande ) hasta que la punta del nozzle esté a 0.2mm del cristal, para ellos deberemos poner entre el cristal y el nozzle una hoja de papel doblada. El papel debe pasar entre los dos rozándolos.
6. Seguidamente desplazaremos el nozzle hacia el tornillo de sujeción de la parte delantera, para ello iremos nuevamente a : Prepare > Move axis > 1mm > Move X y lo desplazaremos a X:
+060.0mm y en el menú anterior Y: -060.0mm.
7. Repetiremos el proceso de nivelación con el papel doblado para
este tornillo.

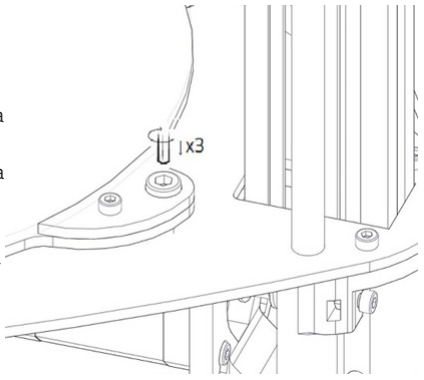
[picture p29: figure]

8. Después desplazaremos el nozzle hacia el tornillo de sujeción de la parte trasera, para ello en X: +045.0mm y Y: +060.0mm.
9. Nivelar esté último tornillo de la base con el papel doblado de la misma forma.
10. Después desplazaremos el nozzle hacia el tornillo de sujeción que hemos nivelado en primer lugar, para nivelarlo nuevamente, para ello iremos a X: -085.0mm y Y: +000.0mm.
11. Nivelar esté último tornillo de la base con el papel doblado de la misma forma.

x 0

z
y

### Carga y descarga de filamento

Una de las operaciones más habituales en nuestra BCN3DR será la carga y descarga de filamento, por varias razones: un cambio de color, empezar una bobina nueva, realizar una limpieza, realizar mantenimiento etc.

- Descarga:
1. Calentar el extrusor. Para ello seleccionar en el menú Preheat PLA.
2. Desde Prepare>Move axis> 1mm>Extruder, hacer avanzar el tornillo de extrusión (sentido positivo) y extruir unos milímetros de filamento. (Es necesario esperar a que el extrusor llega a como mínimo 150ºC para poder mover este motor). Éste procedimiento ayudará a prevenir atascos.
3. Desde Prepare>Move axis> 1mm>Extruder, hacer retroceder el tornillo del extrusor(sentido negativo) 100mm hasta que libere el extremo del filamento.
4. Aflojar los dos tornillos del balancín (idler) situados en el extrusor.
5. Extraer manualmente todo el filamento del tubo bowden.
- Carga:
Una vez con el hilo fuera, deberemos desconectar el tubo bowden del conector del hotend. para ello lo más fácil es:
1. Apretar el tubo bowden hacia el hotend (hacia abajo).
2. Con la mano mantener el pasador metálico del conector hacia abajo pero sin aprisionar el tubo bowden.
3. Estira del tubo con la otra mano y extraerlo del conector.
4. Aflojar los dos tornillos del balancín (idler) situados en el extrusor
5. Realizar un Preheat PLA y introducir el filamento por todo el tubo bowden hasta que sobresalga 20 mm del otro extremo
6. Con la ayuda de las alicates introducir el hilo de plástico dentro del hotend hasta que se extruya filamento por el nozzle. Si es necesario empujar más filamento dentro del tubo con la mano desde el extrusor.
7. Una vez tengamos todo el nozzle lleno de filamento de plástico, cogeremos con una mano el extremo que sobresale por el extrusor e iremos estirando el hilo hacia a fuera y al mismo tiempo con la otra mano introducimos el tubo bowden dentro del conector.
8. Cuando el tubo bowden esté firmemente cogido por el conector apretaremos ligeramente los tornillos del idler con la mano.
9. Con estos pasos tendremos el filamento cargado y listo para imprimir.

### Trabajando con la BCN3DR

A continuación se muestra el diagrama de funcionamiento de la BCN3DR, des del principio al fin. Como se puede comprobar, existen dos caminos posibles que se comentarán en los apartados siguientes:

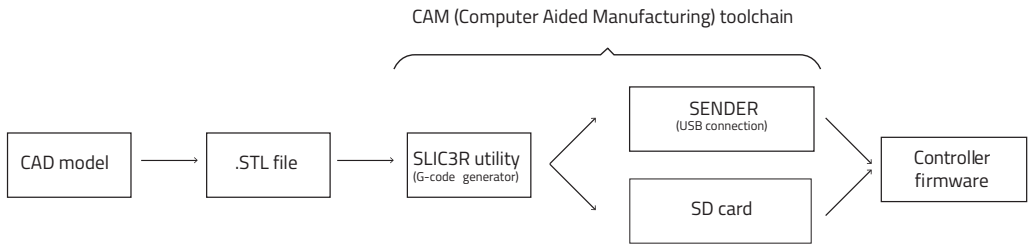
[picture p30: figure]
CAD model; .STL file; SLIC3R utility (G-code generator); SD card; Controller firmware; CAM (Computer Aided Manufacturing) toolchain; SENDER (USB connection)

### 4. CONTROL LCD

La BCN3DR se puede operar desde su menú LCD. El control se realiza a partir de un único botón que combina dos movimientos: el giro y la pulsación.

- Girar el botón para desplazarse por el menú.
- Pulsar el botón para seleccionar la opción deseada.

Junto al botón de control existe un botón de emergencia de color rojo, que permite detener la máquina en caso de mal funcionamiento. Este botón detiene la máquina, aunque deja la pantalla y los ventiladores activos. Una vez pulsado no se puede recuperar el funcionamiento de la máquina, hasta que la máquina se reinicie automáticamente.

### Pantalla principal

La pantalla principal informa del estado de la máquina en ese momento, y del estado de la impresión en curso.

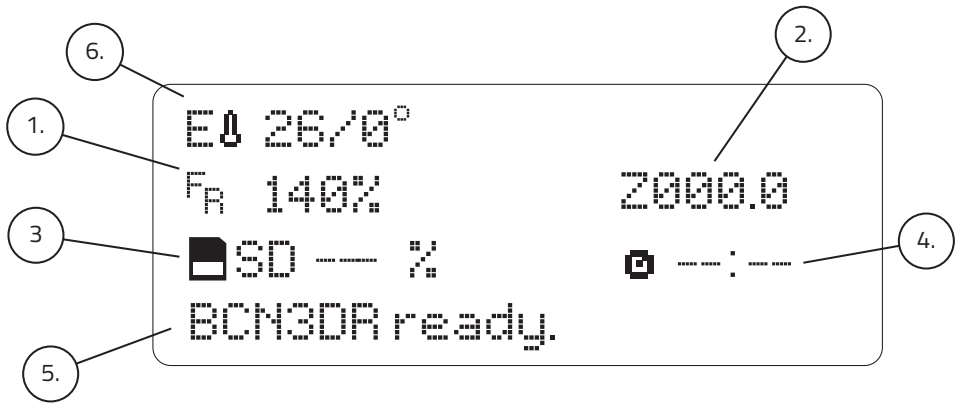
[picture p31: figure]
SD BCN3DR ready.

1. Velocidad de impresión (Fr)
2. Indicador de altura de impresión (Z)
3. Indicador de tanto por ciento de lectura del programa de impresión (SD)
4. Tiempo transcurrido
5. Mensajes de información
6. Temperatura objetivo/real del extrusor

Temperaturas objeivo y real
En la parte superior izquierda pueden visualizarse 2 valores de temperatura. Éstas indican las temperaturas objetivo (arriba), y las temperatura real medida por el termistor (abajo) del extrusor (hotend).

Velocidad de impresión (Fr)
En el lado izquierdo a media altura se encuentra la información de velocidad de impresión. Por defecto este valor es 100%, indicando que se está imprimiendo a la velocidad especificada en el programa de impresión que se está ejecutando.

Este valor es modificable en cualquier momento (incluso sin estar imprimiendo). Para ello, girar el botón de control. De esta manera, con un valor de 150% se imprimirá 1,5 veces más rápidamente de lo que se haya estipulado en el programa de impresión.

NOTA: Al variar la velocidad de impresión se modifican todas las velocidades de los motores, de una manera proporcional y directa al valor de velocidad de impresión, y solo se afecta a las velocidades de los motores (ejes X Y Z y extrusor) y no a la temperatura. Por este motivo, se pueden generar problemas de impresión si se incrementa o decrementa la velocidad en gran medida. Se recomienda no variar este valor en más del 50%.

Indicador de altura de impresión (Z)
En la parte derecha se indica la altura actual del cabezal de impresión.
NOTA: Este dato puede ser incorrecto si la impresora se acaba de encender. En ese momento se indicará Z= 0 pero la altura del eje normalmente será diferente a 0 (estará a la altura a la que se haya parado la impresora anteriormente).

Indicador de tanto por ciento de lectura del programa de impresión (SD)
En la parte inferior se indica el tanto por ciento leído del programa. Nótese que este parámetro hace referencia al tanto por ciento de líneas realizadas del programa Gcode, y no al tanto por ciento de realización de la pieza.

Tiempo transcurrido
En la parte inferior derecha se encuentra el tiempo transcurrido desde que se dio la orden de empezar a imprimir.

Mensajes de información
En la última línea se mostraran diferentes mensajes informando de los procesos que está llevando a cabo la máquina.

### Pantalla de menú

Para entrar al menú interno de la máquina, pulsar el botón giratorio desde el menú principal.

En este menú se encuentran tres opciones: Prepare, Control y Printfrom SD o No SD (según si la SD ha sido insertada en la ranura).

http://www.reprap-electronics.de/

Menú prepare

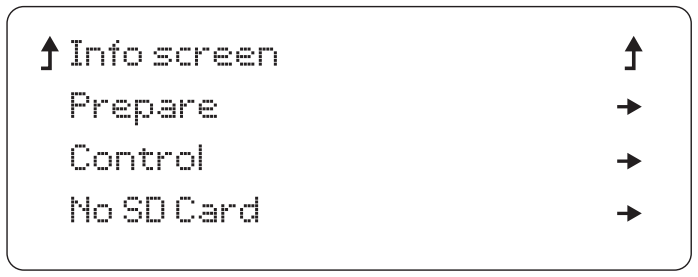
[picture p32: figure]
Info screen; Prepare; Control; No SD Card

El menú Prepare sirve para operar la máquina sin estar imprimiendo. Se encuentran las siguientes opciones:

- DisableSteppers: Esta opción retira la tensión en los motores, facilitando el movimiento manual del cabezal de impresión.
- Autohome: Esta opción posiciona el cabezal de impresión en el origen.

NOTA: Antes de pulsar esta opción, debe asegurarse que nada obstaculiza el movimiento de todos los ejes.

- Preheat PLA: la máquina se precalienta hasta la temperatura de funcionamiento para dicho material.
- Cooldown: Corta la corriente en las resistencias, y los elementos calefactores dejan de calentar.

NOTA: La máquina se enfría de manera natural, por lo que las partes calientes pueden seguir quemando.

- Move Axis: Este menú está destinado al movimiento de los ejes. Seleccionar en primer lugar la distancia que se quiere mover, y a continuación un eje. Para desplazar el eje, girar el botón de control. Rotar hacia la derecha para avanzar en sentido positivo, rotar a la izquierda para avanzar en sentido negativo.

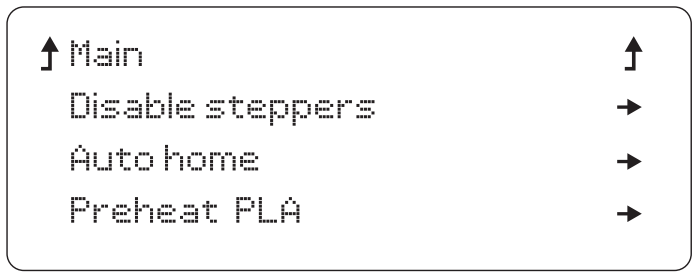
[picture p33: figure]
Main; Disable steppers; Auto home; Preheat PLA

NOTA: Antes de pulsar esta opción, debe asegurarse que nada obstaculiza el movimiento de todos los ejes. El eje E no se moverá si el extrusor está a menos+ de 150ºC.

Menú control
El menú Control permite modificar los parámetros de la impresora antes y durante la impresión. Son parámetros mucho más específicos, que requieren un conocimiento más profundo de lógica de control.

Print from SD /No SD

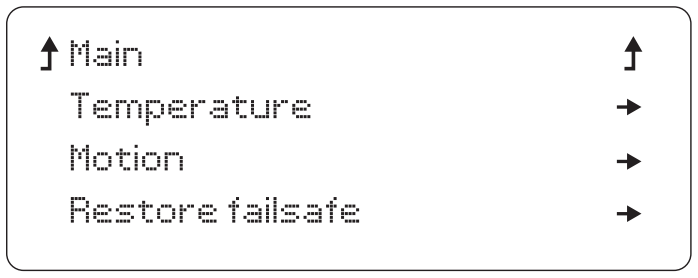
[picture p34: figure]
Main; Temperature; Motion; Restore failsafe

Permite acceder a la memoria SD y seleccionar un archivo almacenado para ponerlo a imprimir. Si la tarjeta no está conectada se muestra el texto No SD. En este caso se debe conectar la BCN3DR a un PC mediante conexión USB (ver apartado Imprimir).

Print from SD | Print from USB

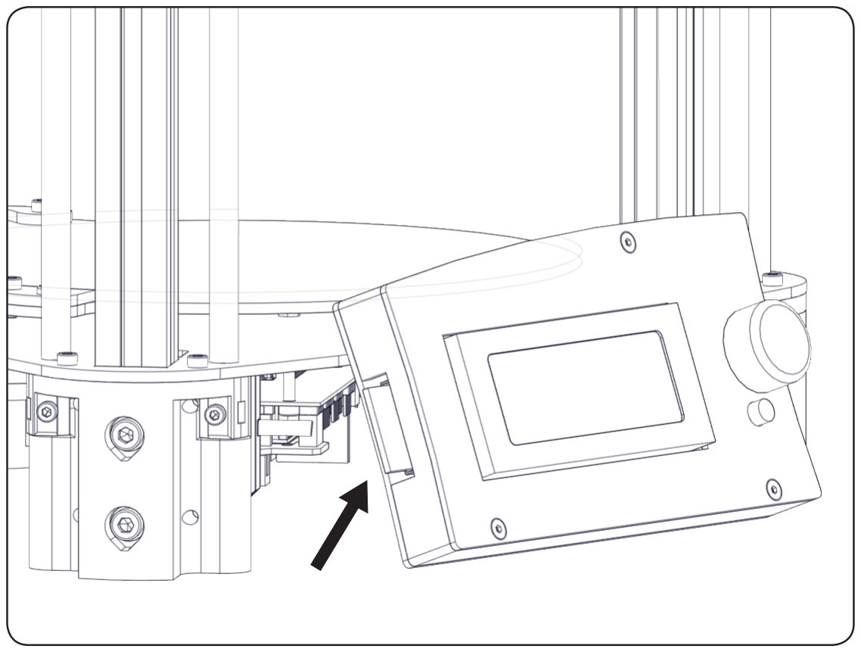
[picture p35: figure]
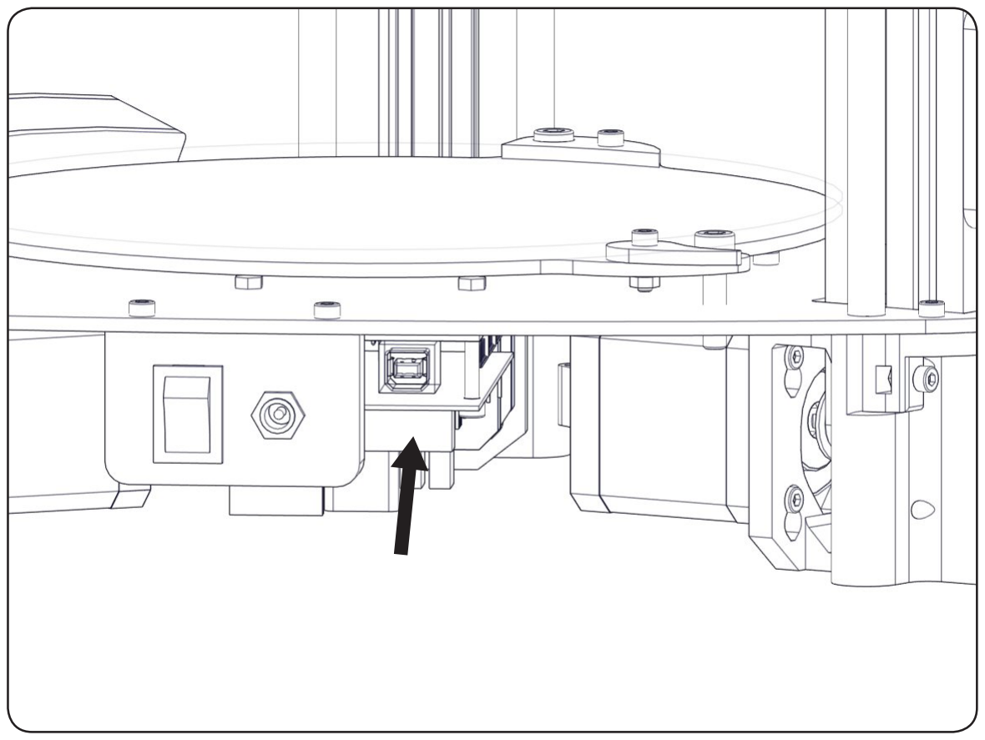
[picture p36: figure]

A modo de referencia, a continuación se muestra el diagrama de menús completo:

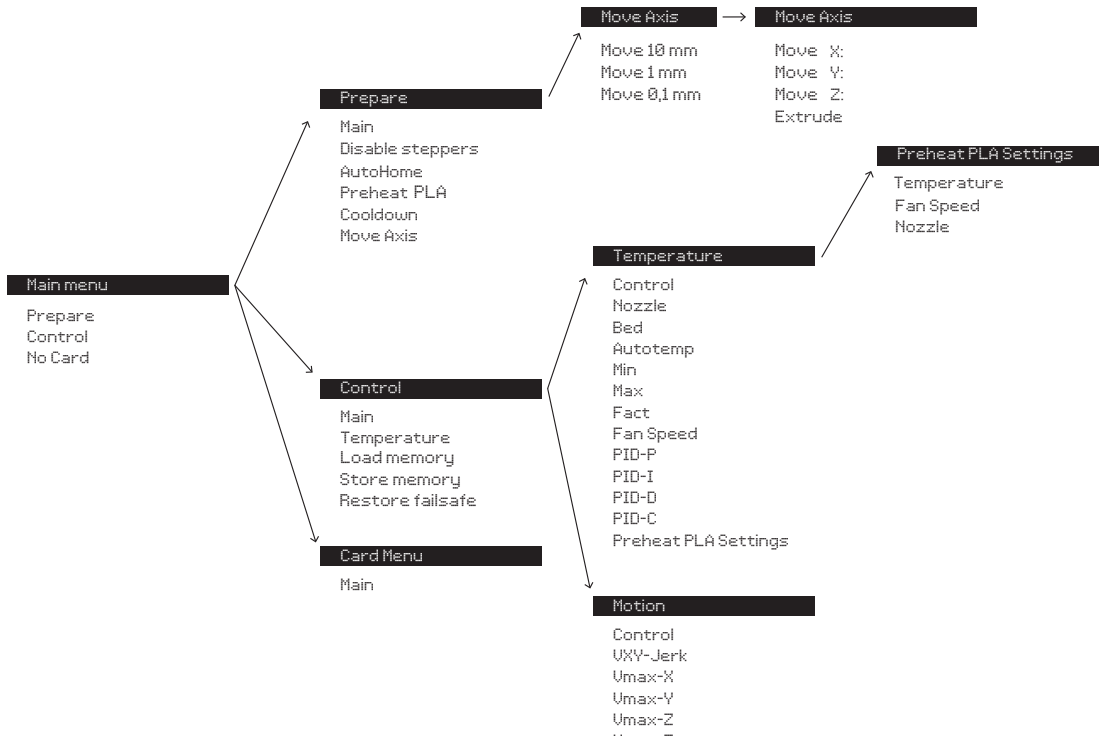
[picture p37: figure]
Prepare Control No Card; Main menu; Main Disable steppers; AutoHome Preheat PLA Cooldown Move Axis; Prepare; Fan Speed Nozzle; Control Nozzle; Autotemp Min Max Fact Fan Speed PID-P PID-I PID-D PID-C Preheat PLA Settings; Temperature; Control; Vmax-Y Vmax-Z; Motion; Main Temperature; Main; Card Menu; VXY-Jerk Vmax-X; Move Axis; Bed; Move; Move X:; Y: Z: Extrude; Move 10 mm Move 1 mm Move 0,1 mm; Preheat PLA Settings; PLA; Load memory Store memory Restore failsafe

### 5. ARCHIVOS .STL

El elemento principal para poder imprimir con la BCN3DR son los archivos de modelos en 3D.

El tipo de archivo más usado para imprimir en 3D es el formato *.STL. Este formato representa las figuras 3D mediante caras planas triangulares. Cuanto más pequeños sean los triángulos, mayor es la resolución y el detalle del modelo 3D.

### Obtención de archivos .STL

Existen tres vías para obtener modelos 3d para imprimir:

1) Diseño propio: El usuario crea sus objetos con un software de modelado 3D. Es una opción interesante si se tienen conocimientos de modelado.
Existe una amplia oferta de programas, algunos de ellos son gratuitos (OpenSCAD, FreeCAD, Blender), mientras que otros requieren licencia comercial (SolidWorks, Rhinoceros, Inventor etc.). En general todos ellos permiten guardar/ exportar los archivos en formato STL.

Vmax-E
Vtrav-min
Vmin
Amax-X
Amax-X
Amax-X
Amax-X
Aretract
Xsteps/nn
Ysteps/nn
Zsteps/nn
Esteps/nn

2) Descarga: Actualmente existen numerosos repositorios o “almacenes” online, donde la comunidad comparte sus modelos 3D con los demás usuarios. A modo de ejemplo se citan los siguientes:
- www.grabcad.com – Repositorio especializado en modelos de ingeniería, diseño y arquitectura. Los modelos 3D no siempre se encuentran en formato STL, sino en el formato del software usado por el usuario que ha creado el modelo.
- www.thingiverse.com – Repositorio creado por la empresa MakerBot, cuenta con una gran cantidad de modelos en formato STL y herramientas de customización de algunos diseños.
- www.rascomras.com – Primer repositorio 3D en español.
3) Digitalizado: Paralelamente al desarrollo de la impresión 3D, la tecnología de escaneado 3D doméstica está evolucionando a gran velocidad. En este sentido, se recomienda visitar la web http://www.123dapp.com/catch de Autodesk. En ella se proporcionan herramientas gratuitas para obtener modelos digitales a partir de imágenes tomadas con cámara fotográfica.
Otros métodos existentes son: software especializados que combinan el uso de proyectores y cámaras, o escáneres 3D.

### Edición y reparación del .STL

Como se ha comentado, un archivo en formato *.STL no siempre se encuentra en buen estado. Algunos errores comunes son:

- Agujeros. El modelo a imprimir debe estar cerrado, sin agujeros.
- Orientación de las caras. Como hemos dicho, un modelo STL se compone de caras planas. La orientación de todas las caras debe ser la misma y hacia afuera de la pieza. En otras palabras, no puede ser que unas caras “miren” en un sentido y otras en otro, todas deben apuntar hacia afuera. Esto sucede de manera accidental al trabajar con los software de modelado.

Existen varios software para editar y reparar archivos STL corruptos. RepRapBCN recomienda Netfabb, que en su versión gratuita BASIC permite realizar las operaciones básicas de edición (escalar, rotar, cortar, combinar, etc.), reparación y medición.

http://www.netfabb.com/downloadcenter.php?basic=1

A continuación se describe la información esencial para la edición de archivos STL en Netfabb. Se recomienda consultar la página oficial para tener un conocimiento más profundo.

### Interfaz de Netfabb

Tras la instalación de Netfabb, es conveniente familiarizarse con su interface. En primer lugar, se habilitará la visualización del volumen de impresión de la BCN3DR. Para ello, clicar en View/Show Platform.

A continuación, se redefinen las dimensiones del volumen. Clicaremos Settings/Settings/General/Default PlatformSize. Allí se introducen los valores que corresponden a la BCN3DR: 170 x 170 x 180. Finalmente, clicar en Save.

En la barra de herramientas superior se observan diversos bloques de botones, de los que se destacan:

1) 7 vistas básicas
2) Herramientas de zoom
3) Herramienta de orientar una cara con el plano inferior
4) Herramienta de Mover, Rotar y Escalar
5) Herramienta de reparación

En la parte derecha de la pantalla se dispone la información básica del modelo y la herramienta de corte.

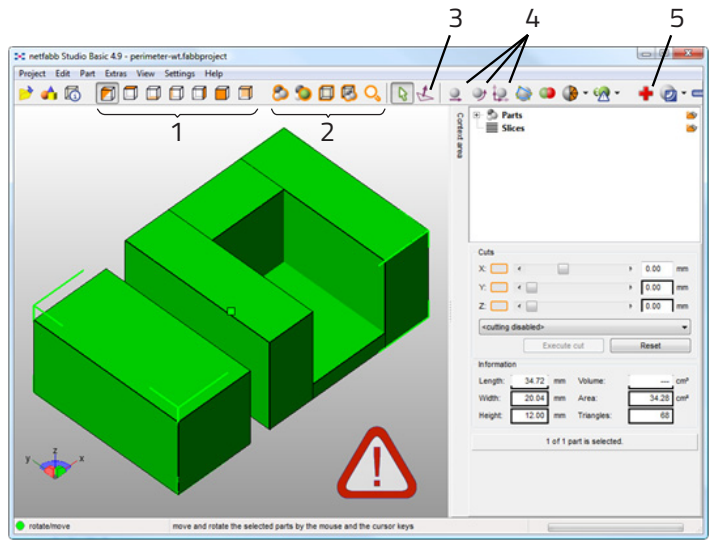
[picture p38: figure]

### Reparación

En caso de que la pieza necesite ser reparada, una señal de advertencia aparecerá en la parte inferior derecha de la ventana. Para reparar el modelo, seleccionar el modelo y clicar en la herramienta Repair.

- A continuación, en la ventana de la derecha, clicar en Automatic Repair, y en la ventana emergente seleccionar Default Repair. Clicar en Execute, y para finalizar, clicar en Apply Repair en la ventana de la derecha.
En la ventana emergente, seleccionar la opción Remove old part para eliminar el archivo original con errores. Si el archivo se ha reparado satisfactoriamente la señal de alerta habrá desaparecido.
- En caso de que el error sea que las caras de la figura están invertidas, el modelo se mostrará todo en color rojo. En este caso, el modelo se puede reparar desde Part/InvertPart.

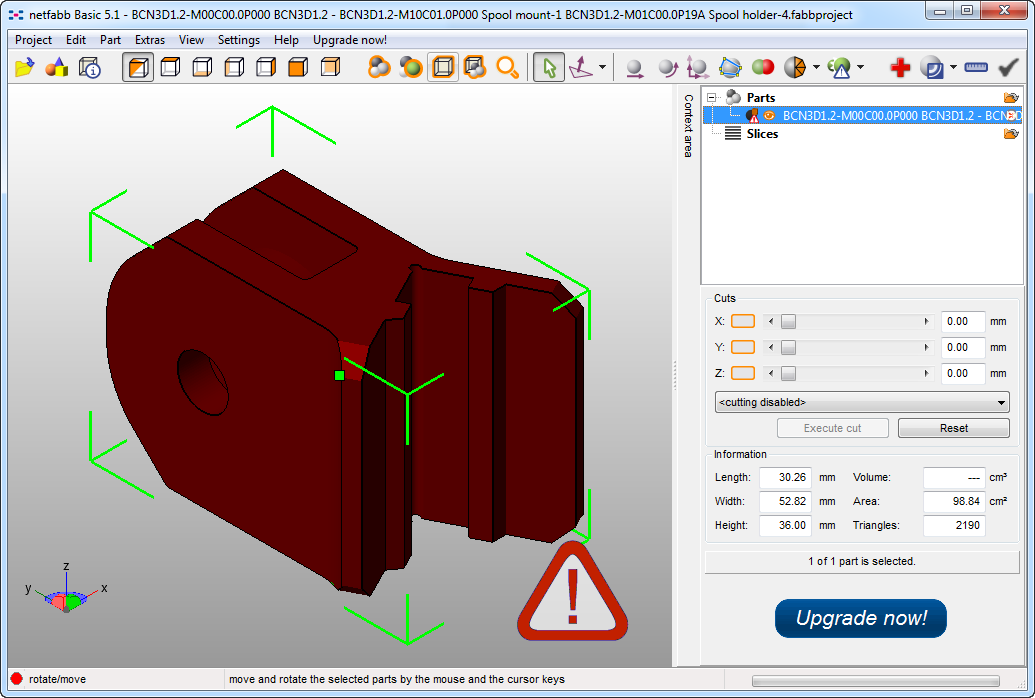
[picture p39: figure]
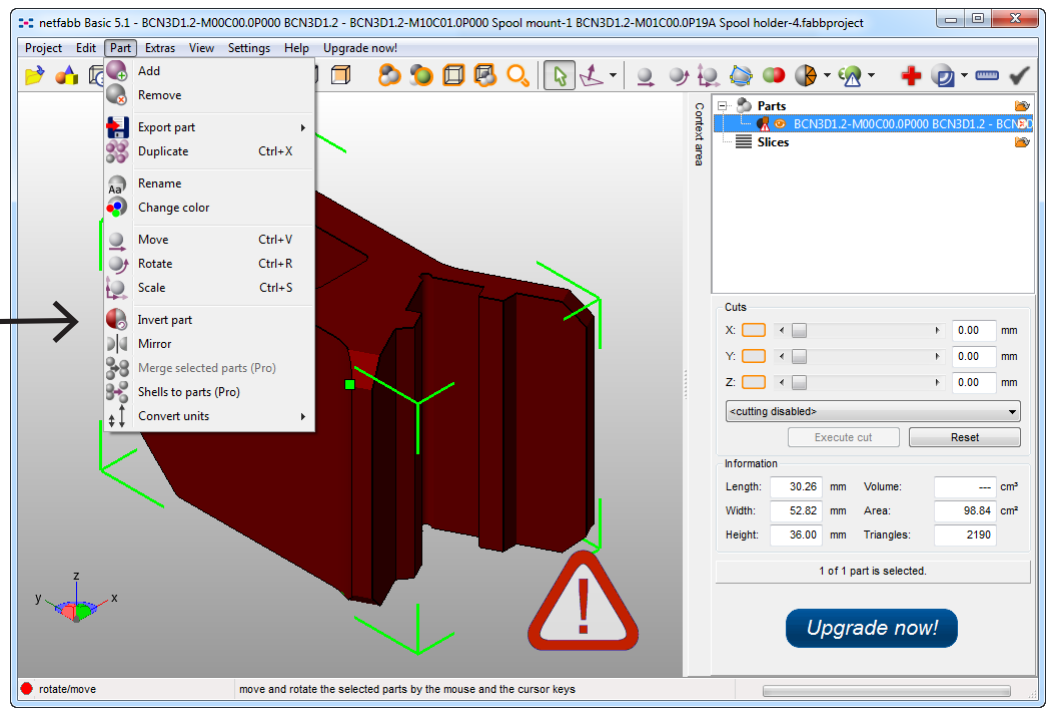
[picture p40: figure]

### Orientar y mover a origen

En primer lugar, se necesita orientar correctamente la pieza, generalmente sobre una cara plana. Para ello, el método más sencillo es seleccionar la herramienta de orientar una cara con el plano inferior (align to bottom plane) y hacer doble clic sobre la cara que estará en contacto con la base de la impresora.

A continuación, se debe mover la pieza al origen. Para ello, seleccionar el modelo (figura en color verde) y usar la herramienta Move. En la ventana emergente, clicar en To origin y luego en Translate para finalizar.

Otras ediciones adicionales que se pueden aplicar son cortar la figura o escalarla.
Una vez el modelo está reparado y editado ya se puede guardar. Para ello, ir a Part/ExportPart/as STL y guardar con el nombre deseado.

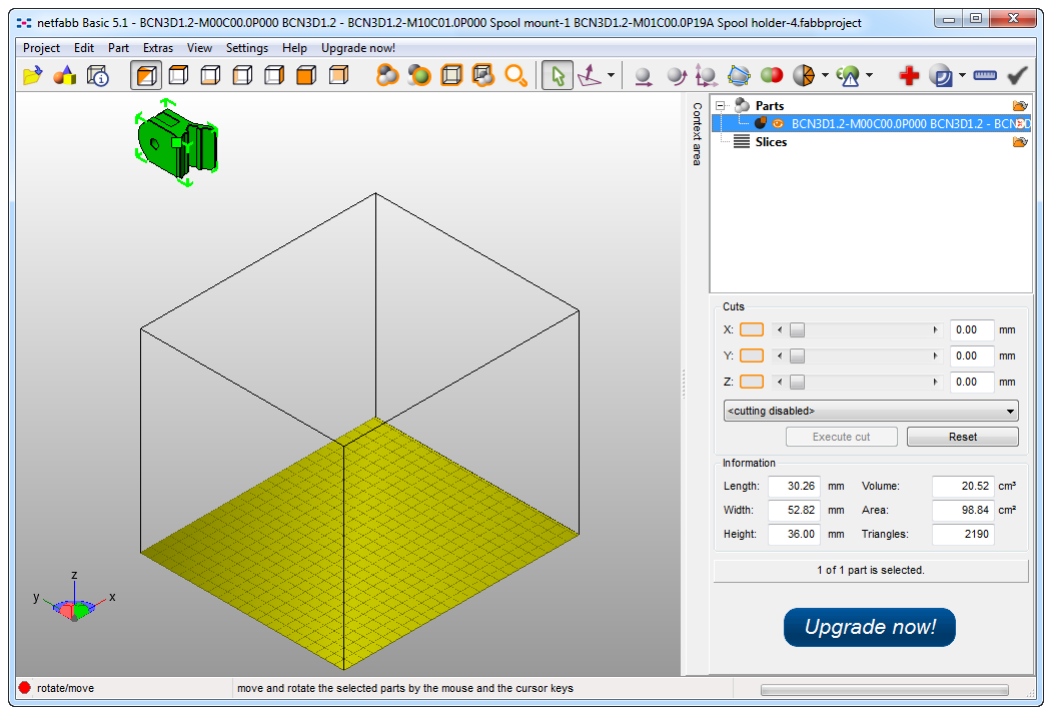
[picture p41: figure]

### Generación del G-CODE

Llegados a este punto, ya se dispone de un modelo 3D listo para imprimir. Sin embargo, es necesario un último paso. Se debe convertir el archivo en formato*.STL a un archivo que la impresora pueda entender para fabricar el modelo. En otras palabras, se debe generar el archivo de Gcode.

El Gcode es un lenguaje informático usado para controlar máquinas de CNC, incluidas la mayoría de impresoras 3D. Se trata, básicamente, de una lista de instrucciones que indican las posiciones y velocidades a las que se debe mover cada uno de los ejes, y la temperatura del hotend.

Existen diversos software para generar un archivo Gcode a partir de un archivo STL. RepRapBCN recomienda el uso de Slic3r, un software open source que, versión a versión, introduce nuevas funcionalidades y mejoras.

http://slic3r.org/download

Igual que otros software para generar GCodes, Slic3r secciona el modelo 3D en capas, que posteriormente se depositarán para generar el diseño en 3D. En cada capa, se establece una diferencia entre los perímetros y el relleno de la pieza. Además, se puede escoger la secuencia de operaciones, velocidad de impresión, número de perímetros, etc. Dado que hay multitud de parámetros, algunos de cierta dificultad de comprensión, se han preparado configuraciones específicas para facilitar el proceso al usuario novel.

### Configuración del Slic3r

Los siguientes perfiles de impresión se han preparado para la BCN3DR con una boquilla de 0,4mm, teniendo en cuenta el tipo de pieza a imprimir y su uso posterior.
Éstas deben servir como punto de partida y pueden ser mejoradas para ir más deprisa, conseguir un mejor acabado, etc.

Se describen a continuación:

ST: Configuración estándar con altura de capa de 0,2mm para la mayoría de construcciones.

HQ: Configuración estándar de alta calidad con altura de capa de 0,1mm para la mayoría de construcciones.

HS: Configuración pensada para trabajos en los que necesitamos obtener el modelo de una forma rápida, sin perder mucha calidad.

SV: Configuración especial para piezas tipo envase. No hay relleno y la pieza se va fabricando en espiral con una única superficie, mejorando el acabado superficial.

WALL: Configuración especial para piezas con geometrías muy “exóticas”, como las que se generan con el algoritmo Voronoi (con su máximo exponente en el diseñador Dizingof). No tiene relleno, y se baja la temperatura y velocidad para mejorar los voladizos.

### Uso básico del Slic3r

A continuación se comentan los aspectos esenciales para el uso de Slic3r. Para un conocimiento profundo de la aplicación, se recomienda leer el manual oficial, disponible en la página web del proyecto:

http://manual.slic3r.org/

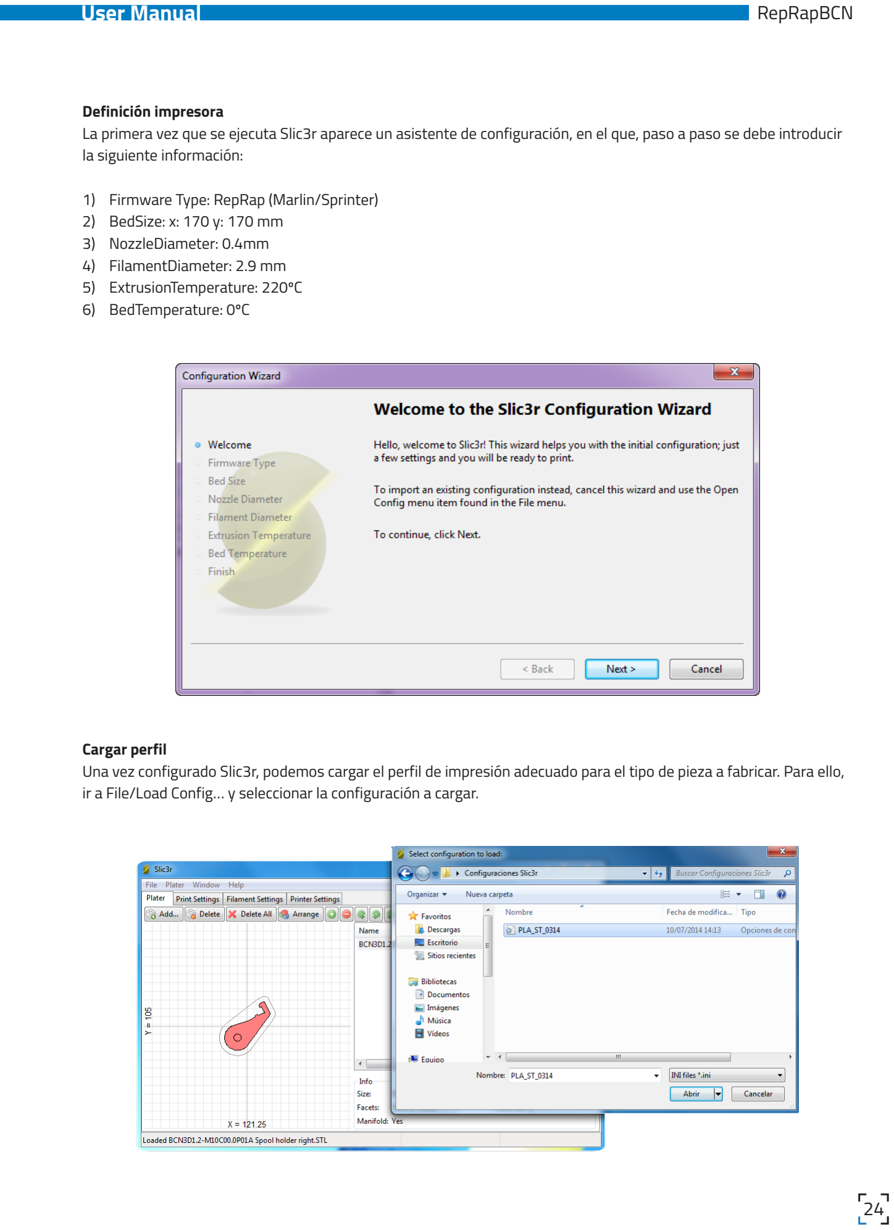
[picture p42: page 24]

Definición impresora
La primera vez que se ejecuta Slic3r aparece un asistente de configuración, en el que, paso a paso se debe introducir la siguiente información:
1) Firmware Type: RepRap (Marlin/Sprinter)
2) BedSize: x: 170 y: 170 mm
3) NozzleDiameter: 0.4mm
4) FilamentDiameter: 2.9 mm
5) ExtrusionTemperature: 220ºC
6) BedTemperature: 0ºC

Cargar perfil
Una vez configurado Slic3r, podemos cargar el perfil de impresión adecuado para el tipo de pieza a fabricar. Para ello, ir a File/Load Config… y seleccionar la configuración a cargar.

Añadir archivos
A continuación, añadir los archivos STL previamente editados y reparados. Se pueden arrastrar directamente sobre la plataforma, o clicar en el botón Add…Se pueden añadir tantos archivos diferentes como se quiera.

Además, se puede imprimir más de una copia. Tan solo es necesario marcar el contorno de la pieza a duplicar (o seleccionarla en la lista de la derecha) y clicar el botón + tantas veces como se desee.

Exportar Gcode
Una vez las piezas se han dispuesto en la plataforma y la configuración se ha ajustado, ya se puede exportar el Gcode. Para ello, pulsar el botón ExportGcode… e indicar la ubicación de guardado y un nombre. Se habrá creado un archivo con extensión *.gcode.

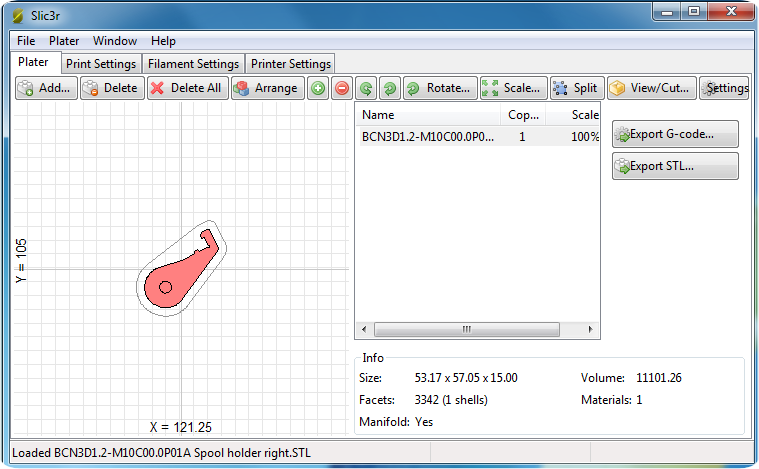
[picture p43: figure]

El proceso de generación del Gcode puede tardar, en función de la complejidad del modelo 3D y de la configuración escogida. Así mismo, la potencia del ordenador es determinante. La duración del proceso está comprendida entre los 10s hasta los 15 minutos en las piezas más complejas.

### Transferencia del G-CODE a la BCN3DR

Finalmente, tan solo hace falta transferir el Gcode a la impresora para iniciar la impresión. Para ello, existen dos procedimientos distintos, en función de la comodidad para el usuario y de la disposición de la impresora y el ordenador:

1) Mediante pantalla LCD. Usar una tarjeta SD, cargada con el archivo Gcode a imprimir e introducirla en la ranura lateral de la pantalla de la BCN3DR. Una vez insertada, pulsar el botón de control y escoger la opción Printfrom SD para seleccionar la pieza.
2) Conexión al pc. Usar un software para conectar la impresora al ordenador a través de USB. Desde RepRapBCN recomendamos RepetierHost http://www.repetier.com/download/

Un software abierto y gratuito que, además, permite visualizar los STL, monitorizar el progreso de impresión y cargar STL, generando automáticamente los Gcodes a través de configuraciones precargadas.

Una alternativa más simple a RepetierHost es el software PrintRun https://github.com/kliment/Printrun

### 6. IMPRESIÓN DESDE TARJETA SD Y USB

En la tarjeta SD que acompaña a laBCN3DR se encuentran unos archivos 3d precargados, para realizar las primeras impresiones. A continuación se describen las características de cada figura:

- Cubo: El cubo es la figura ideal para comprobar si la calibración y configuración de la máquina es correcta. Consiste en un cubo de 20mm de lado con un relleno de un 25%. Permite comprobar el paralelismo y la precisión dimensional de la impresora.

Material: PLA
Altura de capa: 0,2mm
Tiempo de construcción: 15minutos
- Torre: La torre es un buen ejemplo de pieza con detalle. Los ladrillos del exterior y los peldaños de la escalera interior, junto con el espiral central, permiten comprobar la calidad de la impresión.

Material: PLA
Altura de capa: 0,1mm
Tiempo de construcción: 2horas 15minutos

Una vez escogida la pieza que se quiere imprimir, y tras haber calibrado la máquina y comprobado que todo funciona correctamente, se debe proceder de la forma siguiente:

- Asegurarse de tener cargado el material PLA en la impresora

- Precalentar la impresora mediante los comandos siguientes de la pantalla LCD:

Menú principal > Prepare > Preheat PLA

- Una vez alcanzada la temperatura de trabajo en el extrusor, hacer un purgado del material:

Menú principal > Prepare > Move axis > 1mm > Extruder

Girando la rueda en sentido horario unos pocos milímetros, hasta que salga material de forma continua por la boquilla. Luego retirar el material extruido.

- Insertar la tarjeta SD en lado izquierdo del módulo de la pantalla, prestando atención a la posición de la tarjeta y vigilando de no introducirla por el orificio posterior
- Iniciar la impresión seleccionando el archivo deseado:

Menú principal > Printfrom SD > Nombre_archivo

A partir de aquí la impresora empezará la construcción de la figura. Conviene prestar atención al proceso de fabricación, especialmente durante las primeras construcciones.

### 7. FILAMENTO

La BCN3DR presenta sus mejores resultados de impresión con PLA en formato filamento de tipo plástico de 3mm. A continuación se presenta una breve descripción del material aceptado actualmente:

PLA
El PLA (poliácido láctico) es el material de impresión 3d por excelencia, gracias a su facilidad de conformado mediante FDM. Es el material recomendado para iniciarse en este tipo de tecnología de fabricación. Existe una gran variedad de colores y permite conseguir geometrías complejas sin una gran dificultad. El acabado es ligeramente brillante o semi-mate.

Para la impresión, se trabaja a temperaturas que oscilan entre los 220ºC y los 230ºC, en función del proveedor de material y de la velocidad de impresión. Para la construcción de voladizos se requiere ventilador de capa. Presenta una gran adherencia en la base de cristal.

Las propiedades mecánicas son medias, aunque presenta una cierta fragilidad en piezas que requieren deformación. A partir de una temperatura de trabajo de unos 50º, las piezas pueden presentar deformación. Se disuelve en sosa cáustica.

### 8. FIRMWARE

### ¿Qué es el firmware y cuándo actualizarlo?

El firmware es el software necesario para controlar un hardware. Es decir, es el programa interno que controla la BCN3DR, y permite que desempeñe sus funciones normalmente. La BCN3DR se entrega ya instalada con la última versión del firmware publicada en la web.

Sus funciones básicas son:

Por un lado, interpretar los archivos .gcode que deseamos imprimir a instrucciones útiles para impresión, pulsos en los drivers para mover motores o temperaturas objetivo.

Por otro lado también se encarga que gestionar los periféricos de la máquina como son la pantalla, para poder interactuar con ella sin necesidad de conectarse a un ordenador, o los finales de carrera, necesarios para el correcto funcionamiento de nuestra impresora.

Normalmente el firmware de un dispositivo viene integrado en éste y no es posible modificarlo o cambiarlo por otro a menos que el fabricante quiera hacerlo y lo haya previsto en su momento.

La ventaja de nuestra impresora RepRap es que sigue la filosofía de Open Source de modo que si queremos podemos cambiar o modificar el firmware para adaptar nuestra máquina a nuevas funcionalidades y accesorios o mejorar su comportamiento.

La posibilidad de modificar el firmware queda bajo la responsabilidad de cada usuario. RepRapBCN siempre desarrollará firmware orientado a la impresión con sus productos, y los difundirá libremente para su uso.

Así pues, fuera de las modificaciones puntuales que cada uno decida hacer en su máquina.

### ¿Cuándo es necesario actualizar el firmware?

Será necesario siempre que cambiemos alguna funcionalidad de nuestra máquina que implique un cambio en su sistema de control. Por ejemplo, un nuevo cabezal extrusor, dual extruder, paste extruder, etc…También es necesario si se cambia cualquier componente de nuestra máquina como tamaño de poleas, finales de carrera, termistores, longitud de ejes, velocidades o aceleraciones de impresión…
Finalmente, se puede cambiar el firmware al recibir una actualización de RepRapBCN. En estos casos se anunciará su publicación vía página web y redes sociales, y sus mejoras y novedades respecto la versión anterior.

### Descargar el IDE de Arduino

En este apartado se indican los pasos a seguir para poder actualizar/modificar el firmware controlador le la impresora.

El primer paso consiste en instalar el IDE de Arduino en un ordenador. Este es el programa que nos permitirá interactuar con la tarjeta Arduino de la BCN3DR.

1. Descargar el paquete de software ARDUINO de la web http://www.reprapbcn.com o abrirlo desde el USB subministrado.
2. Instalar el programa.
3. Una vez instalado, conectar la BCN3DR al ordenador mediante un cable usb. De esta manera se establece la conexión con el arduino.

La primera vez que se conecta una placa a un ordenador hace falta instalar los drivers del componente. Si el ordenador no instala los drivers automaticamente al conectar la placa, seguir los pasos explicados en:

http://arduino.cc/en/guide/windows#toc3

4. Abrir la aplicación Arduino
5. Desde el menu Archivo>Abrir, seleccionarla versión de firmware guardada o descargada anteriormente.
El archivo que se debe abrir tiene extensión*.ino, y se encuentran en una carpeta con el mismo nombre, mezclado con todos los subprogramas del firmware.
6. En este momento se pueden modificar los parámetros deseados si es necesario.
7. Seleccionar el modelo de tarjeta Arduino y el puerto desde Herramientas>Tarjeta>Arduino Mega 2560 y Herramientas>Puerto Serial>COM X

- La tarjeta con la que opera la BCN3DR es una Arduino Mega 2560.
- El puerto se refiere al conector dónde tenemos conectada la placa en el ordenador (Puerto COM). Podemos consultarlo en el sistema operativo (Windows) desde Inicio>Equipo>Boton derecho>Propiedades>Administrador de Dispositivos> Puertos COM y LPT.

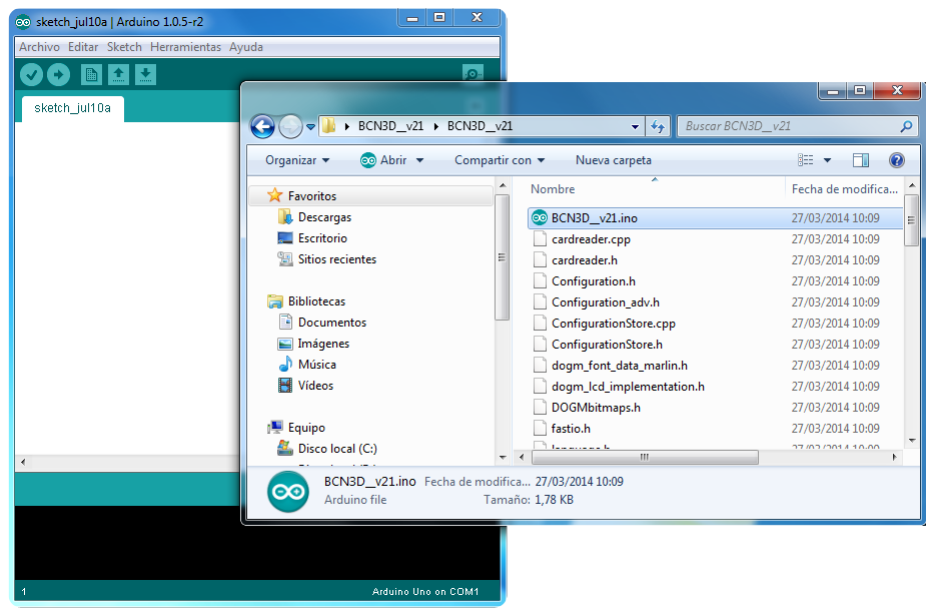
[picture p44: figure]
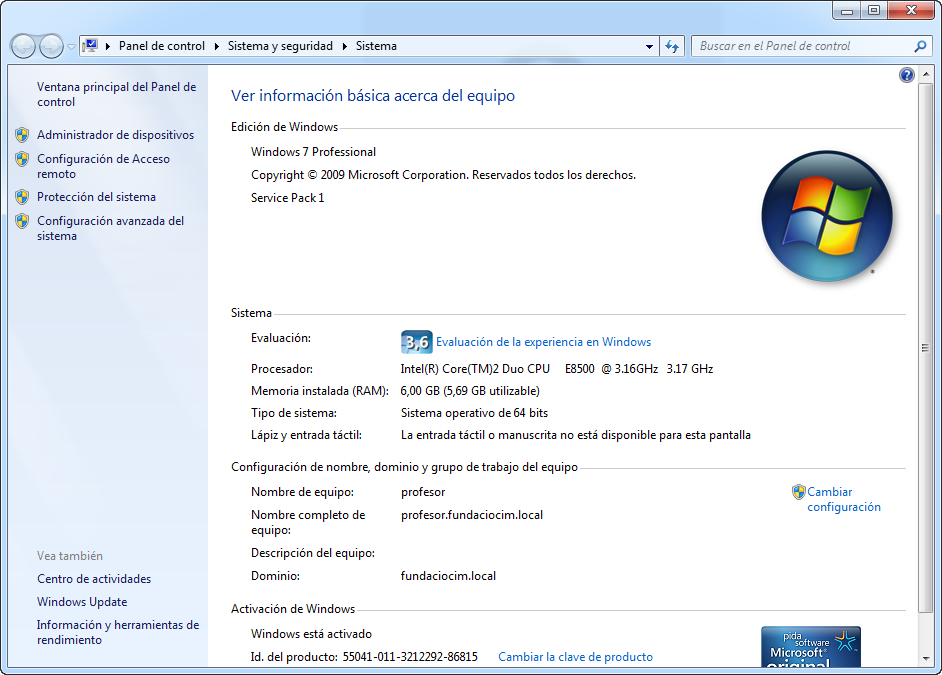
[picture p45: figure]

8. Seleccionar el boton Cargar.

Emprieza la carga, primero con la compilación del programa para detectar errores, y a continuación con la propia carga en la memoria de la placa.
9. Si el proceso termina correctamente se mostrará el mensaje “Carga terminada”, y la impresora estará lista para utilizar.

### 9. SOLUCIÓN DE PROBLEMAS

### Es difícil sacar la pieza una vez acabada

- Con la ayuda de un cúter, colocarlo cuidadosamente debajo de la pieza e ir moviéndolo hasta retirarla por completo.
- Es muy recomendable sacar el cristal de la base aflojando la leva. Si se intenta sacar la pieza directamente sin sacar el cristal de la impresora se puede descalibrar y/o forzar los tornillos que ajustan la altura de la base.

### Un motor no gira correctamente (ajuste de pololus)

Desde el menú de la pantalla LCD Prepare/Move Axis, se puede comprobar si los motores funcionan correctamente moviendo los ejes. Se procederá de la siguiente manera:

1. Antes de nada, mover con la mano el eje de los motores para asegurarse que se mueven, y que no hay nada que entorpezca. Si siguen sin moverse bien, ajustar los pololus como se indica a continuación:
2. Si los motores no se mueven o no se mueven lo suficiente, les falta potencia. Apagar la máquina y girar el potenciómetro del pololu 5 minutos de reloj en
sentido horario.
3. Si los motores se mueven pero en ciertos momentos hacen movimientos
bruscos, es decir, pierden pasos, es que tienen demasiada potencia. En ese caso
hacer lo mismo pero girando el potenciómetro 5 minutos en sentido antihorario.

NOTA: Antes de pulsar esta opción, debe asegurarse que nada obstaculiza el movimiento de todos los ejes. El eje E no se moverá si el extrusor está a menos de 150ºC.

### Se detiene la extrusión

Se puede deber a diversos motivos:
- El motor no gira debidamente:
1. Ajustar la potencia de los pololus.
2. Comprobar que las tuercas del eje del engranaje grande no aprietan contra el extrusor, si no una contra la otra. Asegurarse que el mecanismo gira fácilmente accionándolo con la mano.
3. Comprobar que los cables eléctricos no tenga desperfectos y estén conectados correctamente.
- El hilo no avanza aunque el motor gire:
1. Asegurarse de que la temperatura sea la correcta según el tipo de plástico.
2. Desmontar el extrusor y limpiar bien los orificios de restos de plástico.
3. Subir la temperatura de la máquina al máximo e intentar extruir con la mano con fuerza para que salga el posible atasco.
- El hilo se ha enrollado:
1. Asegurarse que la bobina gira correctamente en el soporte, y que el hilo baja más o menos recto y sin tirones hacia el extrusor. Un hilo enredado puede provocar que se rompa o que la bobina se caiga del soporte.
- Se ha retirado la SD de su alojamiento:
1. Si se retira la SD de la pantalla, la impresión para y no es posible continuar desde el punto donde se paró.

5 min.

5 min.

- En la pantalla aparece el texto “Mintemp” o “Maxtemp”:
1. La temperatura del hotend ha salido de la zona en la cual debe trabajar. Asegurarse de que las conexiones estén bien y el cableado no esté deteriorado.
2. Si el problema persiste, quitar el hotend de la máquina y asegurarse que el termistor no esté roto y los cables no se toquen, lo cual provocaría un cortocircuito y una mala lectura de la temperatura.
- El cristal está demasiado cerca de la boquilla al empezar la impresión:
1. Apretar los tornillos de la base, para que empiece la impresión un poco más arriba y volver a empezar.
2. Volver a calibrar la base.

### La pantalla no responde o no muestra nada

Se puede deber a diversos motivos
- Para realizar los movimiento en los ejes X e Y el Arduino necesita realizar muchos cálculos matemáticos complejos que requieren gran parte de la capacidad de procesado, por esta razón es posible que se produzcan error puntuales en el muestreo de la pantalla. Para solucionarlos:
1. Apretar el botón del menú para acceder al menú principal
2. Seleccionar la opción superior ‘Info screen’ para volver al menú de información anterior.

De esta forma la pantalla se actualizara y volverá a mostrar la información correctamente, si no sucede esto:

1. Apagar la impresora y volverla a encender.
2. Asegurarse que los cables que alimentan la pantalla estén bien conectados. Los dos cables que vienen de la electrónica deben cruzarse.
3. Cargar de nuevo el firmware desde un PC. Si el firmware está mal cargado la pantalla aparecerá en blanco (ver sección 8 Firmware).

### El carro eje X,Y o Z no se desplazan con fluidez

1. Limpiar las guias.

### 10. DIAGNÓSTICO DE LA CALIDAD DE IMPRESIÓN

En este apartado se va a hacer una lista de los problemas de calidadde impresión más comunes, y la manera de corregirlos o minimizarlos.
En cualquier caso, es recomendable utilizar las configuraciones de nuestra web (www.reprapbcn.com), ya que han sido testadas y funcionan correctamente con la mayoría de piezas para imprimir en este tipo de impresoras.

### La pieza se separa de la base caliente (WARPING)

A veces la piezas no se adhieren bien al cristal durante la impresión.

En este caso probar las siguientes soluciones:
1. Limpiar bien el cristal para evitar que el polvo u otras substancias interfieran entre la base y la pieza.
2. Impregnar la superficie de cristal con una capa de laca
3. Calibrar la base de impresión como se explica en el apartado 11 Mantenimiento.
5. Hacer que la primera capa eche más material (desde Slic3r, PrintSettings/Advanced/FirstLayer).

### En la primera capa no extruye material en toda la geometría

1. Puede suceder que la primera capa no se adhiera correctamente al cristal, o no deje un flujo constante de hilo plástico (únicamente una línea de gotas) en toda la figura.

El problema es que la máquina no está calibrada correctamente; el extrusor está demasiado lejos de la base. Revisar el calibrado del apartado 11 Mantenimiento centrándose en el tornillo de regulación de la altura de la superf’icie
de impresión.

### Aparecen grietas en mitad de la pieza

Esto sucede porque la parte de la pieza más cercana al extrusor está más caliente
que las capas inferiores. Si a esto se le suma que el plástico del perímetro se refrigera antes que la parte interior, se generan unas contracciones internas que pueden llegar a separar las capas de la pieza.

Para evitar estas grietas se debe subir 5 grados la temperatura de extrusión, de manera que las capas se adhieran con más fuerza.

### Fused

Al estar trabajando con material fundido, la gravedad hace que éste tienda a gotear desde la boquilla. Se deberán buscar estrategias para minimizar esta problemática, y conseguir mejores acabados superficiales, incluso con geometrías complejas.

### Deposition

El hilo de material que se extruye tiene el diámetro del orificio exterior de la boquilla del hotend. Mediante la deposición del hilo de ese material se debe cubrir, capa por capa, toda la superficie de la pieza a fabricar. Cabe destacar que el proceso de fabricación se produce de modo secuencial, lo cual permite diferenciar entre diversas partes de cada modelo (como por ejemplo, perímetros y relleno) y escoger entre diversas estrategias de impresión (orden, porcentaje y entramado del relleno, etc).

### Aparecen hilillos de plástico alrededor de la pieza

Esto sucede cuando el extrusor se desplaza de un punto a otro sin depositar material.

Para evitarlo, ajustar la opción retract desde Slicer. Esta opción retira parte del hilo del motor del extrusor, de manera que se disminuye la presión del material en el interior del extrusor y se evita el goteo durante el desplazamiento de los ejes. Si se aumenta el retract, se disminuyen los residuos en forma de hilos.

### Modeling

Al ir subiendo en altura, el material imprimido necesita tener un apoyo. Son muchas las piezas que contienen partes suspendidas en el aire (voladizos) o zonas con mucha inclinación, y el material depositado tiene tendencia a desprenderse hasta enfriarse.

Cuando esto ocurra, se recomienda investigar la creación de columnas de apoyo desde el software de impresión (Slic3r).

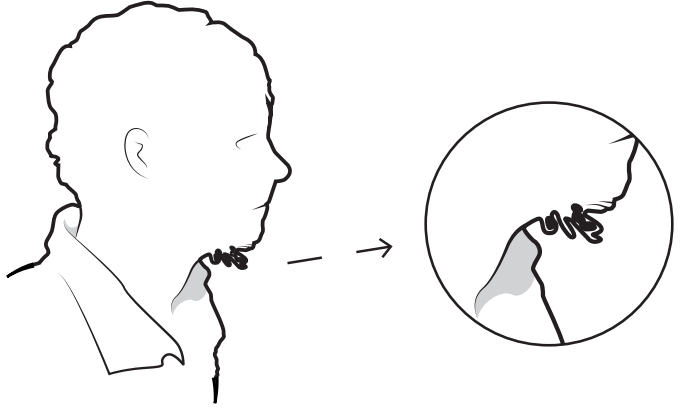
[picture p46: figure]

### Una capa aparece desplazada respecto a la inferior

Cuando en una pieza existe un desfase de posición entre una capa y las siguientes, lo más seguro es que uno de los motores haya perdido pasos. Primero se debe identificar cuál de los ejes se ve afectado, y después ajustar el pololu correspondiente a ese motor, tal y como se explica en el apartado 9 Solución de problemas.

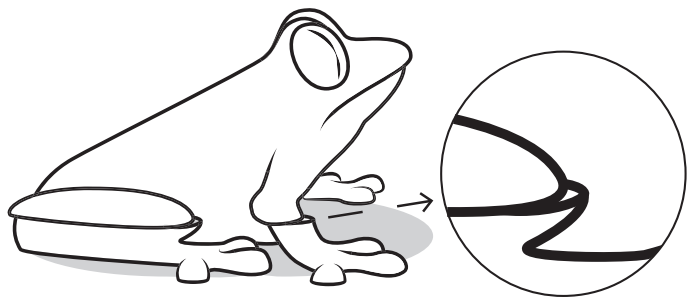
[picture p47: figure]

### 11. MANTENIMIENTO

Dadas las características de la máquina, es muy importante realizar comprobaciones periódicas de las distintas partes, a fin de no perder calidad de impresión y evitar errores.

### Lubricación de las varillas

Se recomienda engrasar las varillas cada cierto tiempo, en especial cuando no se mueven con facilidad o hacen más ruido de lo normal. Para ello se puede usar cualquier tipo de grasa. Colocar unas gotas por las varillas, y mover los ejes para que el mismo mecanismo las reparta por toda su extensión.

### Mantenimiento del filamento

Las bobinas de filamento se deben guardar en un lugar fresco y seco. El calor y la humedad afectan bastante a este tipo de plásticos. Si una bobina no se va a usar durante un largo período de tiempo, guardarla en una bolsa de plástico sellada.

Debe asegurarse que el plástico esté bien enrollado. Una bobina con el plástico suelto puede provocar que éste se enrolle mal, y al imprimir provoque tirones que afectan a la impresión y los componentes de la máquina.

### Limpieza de la base de impresión

Después de varias impresiones, la superfície de impresión se ensucia, y se acumulan capas de laca, polvo y restos de plástico.

Para limpiar el cristal se debe retirar de la impresora. Los restos de laca y polvo se quitan fácilmente poniendo el cristal debajo del agua con un poco de jabón. Si hay restos de plástico enganchados, se pueden retirar con un cúter con cuidado de no rallar el cristal. También se puede usar acetona, ya que diluye el plástico.

### 12. CONSEJOS Y ADVERTENCIAS

Hay ciertos aspectos que creemos hay que tener en cuenta a la hora de utilizar y realizar el mantenimiento de la máquina:

- No verter líquidos sobre el cristal ya que podrían dañar el resto de componentes. Para hacer limpieza de ambos, primero extraerlos de la máquina. Lo único que se recomienda utilizar con la base montada es la laca para una buena adherencia de las piezas.
- Si cuesta retirar las piezas, hacerlo con la base de cristal fuera de la máquina para evitar descalibrarla.
- No sobrecalentar el hotend. Aunque su temperatura está limitada desde el firmware, no utilizar otros métodos para calentarlo por encima de esa temperatura.
- No manipular las partes electrónicas de la máquina cuando está encendida, podría provocar daños en sus componentes.
- No apagar la impresora inmediatamente después de una impresión. Dejar pasar un tiempo para que los ventiladores enfríen sus componentes.

### 13. ASISTENCIA TÉCNICA RepRapBCN

Si no encuentra en este manual una solución a su problema, puede contactar con el equipo de RepRapBCN mediante los siguientes canales:

### Asistencia SAT

Llama al teléfono de nuestro Servicio de Asistencia Técnica: 93 473 88 24.

### Foro

Antes de proceder a cualquier otra acción, se recomienda consultar nuestro foro. Es muy probable otro usuario haya sufrido el mismo problema, y es en el foro dónde se solucionan la mayoría de ellos.

http://www.reprapbcn.com/es/forum

### Correo electrónico

Si el problema no se soluciona, puede comunicarse directamente con nosotros por correo electrónico. Un experto de RepRapBCN buscará una solución lo más rápido posible.

info@reprapbcn.com

### Teléfono

Disponemos de un teléfono de contacto para preguntar directamente a nuestro equipo, o para concertar una cita para traer la impresora hacer una revisión: 93 348 70 25.

Toda esta información se encuentra disponible en nuestra página web, apartado contacto:

http://www.reprapbcn.com/es/contact

En cualquiera de los casos es importante adjuntar el número de serie de la impresora, para tener un registro y saber de antemano los problemas que surjan. También ayuda una fotografía para identificar más fácilmente lo ocurrido.

### 14. GLOSARIO

- Arduino. Plataforma de hardware libre, basadaen una placa con un microcontrolador y un entorno de desarrollo. Es una placa muy popular, y constituye el “cerebro” de la electrónica de la BCN3DR. Necesita que se le cargue el firmware para trabajar.

http://www.arduino.cc/

- Endstop. Final de carrera. Es el componente electro-mecánico que hace contacto con los carros de los ejes, para indicar el recorrido total de estos.

- Filamento. Bobina de cualquier material válido para imprimir.
- Firmware. Código interno de la BCN3DR que gobierna toda su electrónica y permite la impresión. La BCN3DR usa su propio firmware, basado en el popular Marlin.
- Fuente de alimentación. Dispositivo que recibe corriente de la red eléctrica y la adapta a las necesidades de la impresora.
- Gcode. Los archivos en formato Gcode contienen el programa de impresión de las figuras. Se cargan en la memoria SD para que la BCN3DR los pueda leer e imprimir.
- Superficie de impresión. Base de cristal sobre la que se imprimen los modelos.
- Hotend. Extrusor es la parte donde se aporta calor al filamento para derretirlo y poder imprimir.
- Memoria SD. Tarjeta donde se almacenan los archivos en formato Gcode para imprimir.
- Nettfab. Software recomendado por RepRapBCN para editar y reparar archivos STL.

http://www.netfabb.com/downloadcenter.php?basic=1

- Nozzle. Punta del extrusor, salida del material fundido.
- Open Source. Software distribuido y desarrollado libremente. Se focaliza más en los beneficios prácticos (acceso al código fuente) que en cuestiones éticas o de libertad que tanto se destacan en el software libre.
- Pololu. Componente electrónico que regula el buen funcionamiento de los motores de la impresora.
- RepetierHost. Software que permite enviar los archivos Gcode directamente desde el pc a la máquina, mediante un cable USB. Tiene otras funcionalidades, como monitorizar la impresión.

http://www.repetier.com/

- RAMPS 1.4. Su nombre es el acrónimo de RepRapArduino Mega PololuShield. Es una placa electrónica diseñada especialmente para complementar el circuito de la impresora. Contiene unos fusibles para evitar la destrucción de la placa Arduino en caso de sobrealimentación.
- Slicer. Software recomendado por RepRapBCN para generar archivos Gcode a partir de archivos STL.

http://slic3r.org/

- Termistores. Sensores de temperatura. Encontramos uno en el hotend.

### 15. GARANTÍA, DEVOLUCIONES Y POLÍTICA DE SUSTITUCIÓN

Los productos de RepRapBCN no tienen garantía de largo plazo. Todos los componentes de la BCN3DR tienen un año de garantía. Solo se aceptan devoluciones en productos no afectados, dentro de un plazo de 14 días hábiles después de su recepción. Una vez finalizado ese plazo, todas las ventas se considerarán definitivas. Por productos “no afectados” se entiende que el dispositivo no ha sido nunca montado, encendido, programado o de otra forma alterado. RepRapBCN no puede aceptar devoluciones en artículos adquiridos a los cuales se les ha aplicado corriente eléctrica, o han sido de alguna manera programados, modificados o afectados. Sin embargo, ofrecemos piezas de repuesto o servicio técnico sobres los artículos sobre los que se haya probado que contienen defecto de fábrica, y siempre trabajaremos con usted para volver a poner su equipo en funcionamiento.

### 16. TÉRMINOS Y CONDICIONES DE SERVICIO

Toda la información contenida en este manual está sujeta a cambios sin aviso, y se ofrece para fines meramente de conveniencia para el usuario. RepRapBCN se reserva el derecho de modificar o revisar el manual en cualquier momento a su entero criterio. Usted acepta estar sujeto a cualquier modificación y/o revisión. Póngase en contacto con el equipo técnico de RepRapBCN si desea obtener información actualizada.

El diseño de ese manual y todo el texto, los gráficos, la información, el contenido y demás materiales están protegidos por derechos de autor y otras leyes. Ciertas marcas registradas, nombres comerciales, marcas de servicio y logotipos (las “Marcas”) utilizados son marcas registradas y no registradas, nombres comerciales y marcas de servicio de RepRapBCN y sus socios. Ninguna declaración en este manual confiere ni se entenderá como que confiere, por inferencia, impedimento o de otra forma, ninguna licencia ni derecho de usar ninguna Marca sin el permiso por escrito de RepRapBCN. Cualquier uso no autorizado de la información, los materiales o las Marcas podría violar las leyes de derechos de autor, de marcas registradas, de privacidad y publicidad y/u otras leyes y reglamentaciones.

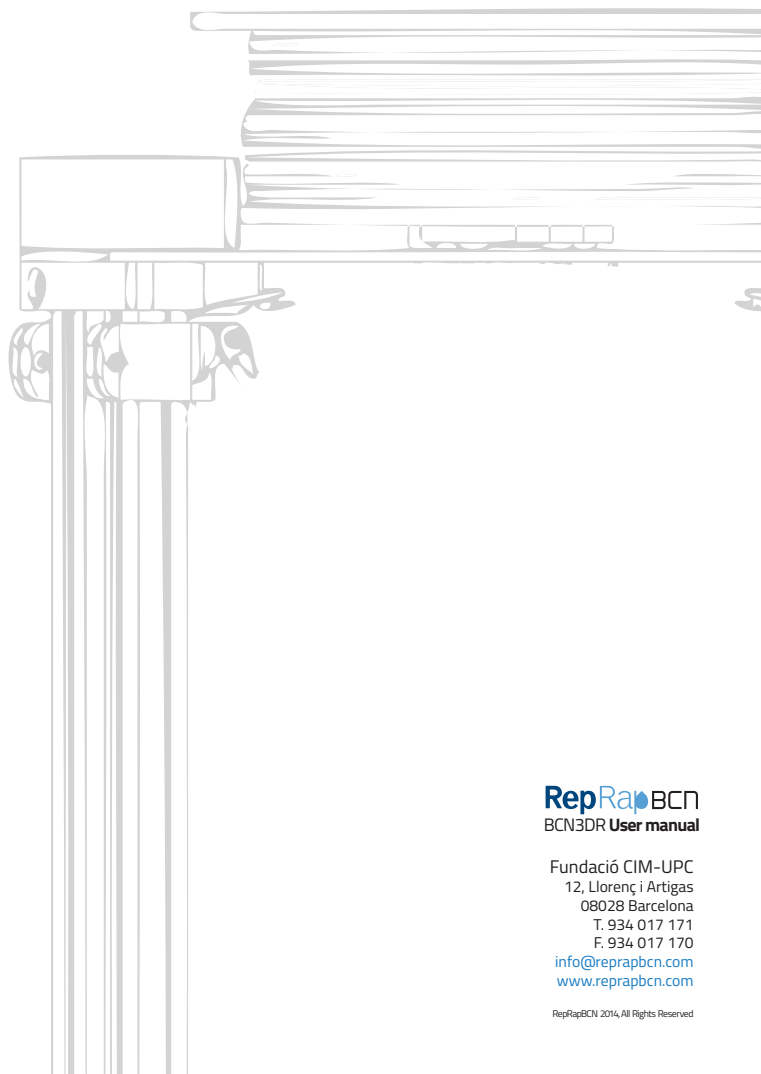
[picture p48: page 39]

BCN3DR User manual
Fundació CIM-UPC
12, Llorenç i Artigas
08028 Barcelona
info@reprapbcn.com
www.reprapbcn.com

RepRapBCN 2014, All Rights Reserved

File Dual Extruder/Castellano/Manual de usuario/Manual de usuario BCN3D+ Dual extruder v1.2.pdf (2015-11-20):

User Manual | RepRapBCN

Dual extruder

### 1. INFORMACIÓN PREVIA

Especificaciones
Tecnología FFF
Conformidad
Seguridad

### 2. PRIMER CONTACTO

Desembalaje
Herramientas y accesorios
Diagrama de la BCN3D+

### 3. PUESTA EN MARCHA

Calibración de la altura de la superficie de impresión Calibración de la distancia relativa
Carga de filamento
Trabajando con la BCN3D+

### 4. CONTROL LCD

Pantalla principal
Pantalla de menú

### 5. ARCHIVOS STL

Obtención de archivos STL
Edición y reparación del STL Interfaz de Netfabb
Reparación
Orientar y mover a origen
Generación del G-CODE
Configuración del Slic3r
Uso básico del Slic3r
Uso del Slic3r para Dual extruder Apuntes y consejos de uso
Uso de Curapara Dual extruder Transferencia del Gcode a la BCN3D+

### 6. IMPRESIÓN DESDE TARJETA SD Y USB

Impresión con un solo extrusor
Qué configuración usar
Superfície de impresión disponible

### 7. FILAMENTOS

PLA, ABS y Nylon
HIPS, PVA, Laybrick, Laywood y Filaflex

### 8. FIRMWARE

¿Qué es el firmware y cuándo actualizarlo? ¿Cuándo es necesario actualizar el firmware? Descargar el IDE de Arduino

### 9. SOLUCIÓN DE PROBLEMAS 10. DIAGNÓSTICO DE LA CALIDAD DE IMPRESIÓN

### 11. MANTENIMIENTO

### 12. CONSEJOS Y ADVERTENCIAS 13. ASISTENCIA TÉCNICA RepRapBCN 14. GLOSARIO 15. GARANTÍA , DEVOLUCIONES Y POLÍTICA DE SUSTITUCIÓN 16. TÉRMINOS Y CONDICIONES DE SERVICIO

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
# INDICE

Material Extrusion Fused Filament Fabrication (FFF) 480mm x 480mm x 455mm
14kg (sin bobinas de filamento)

Ancho: 252mm
Profundidad: 200mm
Altura: 200mm

2

0,1-0,35mm (con boquilla estándar de 0,4mm) 0,2-0,5mm (con boquilla de 0,6mm)

Eje x: 0,05mm
Eje y: 0,05mm
Eje z: 0,1mm

15-35ºC
80ºC (medida en el perímetro) 260ºC
3mm/1,75mm

PLA

Arduino Mega 2560 + RAMPS 1.4

Targeta SD (funcionamiento autónomo) Cable USB (control mediante Repetier Host)

Específico BCN3D+ (basado en Marlin)
STL
Slic3r, Cura
AC 100–240 V, ~4 amps, 50–60 Hz 250W

### 1. INFORMACIÓN PREVIA

### Especificaciones

Tecnología de fabricación: Dimensiones generales:
Peso:

Volumen de impresión:

Número de extrusores:

Altura de capa:

Resolución de posicionado:

Temperatura funcionamiento: Temperatura de cama caliente máx: Temperatura de extrusor máx: Diámetro de filamento:

Materiales admisibles:

Electrónica:

Conectividad:

Firmware:
Archivos compatibles:
Software preparación archivos: Alimentación eléctrica:
Consumo eléctrico:

### Tecnología FFF

La BCN3D+ es una impresora 3D basada en la tecnología FFF (por sus siglas en inglés, Fused Filament Fabrication).

Esta tecnología permite fabricar piezas por medio de la deposición de material fundido.Para ello, se parte de un modelo digital que se secciona en capas finas. El cabezal realiza los movimientos para depositar el material de una capa, luego realiza un pequeño desplazamiento vertical y continua con la siguiente capa. El proceso se repite hasta realizar la figura completa.

la cantidad adecuada de filamento; con un diámetro más pequeño; El filamento es conducido al extrusor; Un bloque calentador funde el filamento a una temperatura manipulable.

La máquina está preparada para incorporar los complementos que publique RepRapBCN, mediante un proceso sencillo y pautado. Uno de los complementos principales es el cambio de cabezal extrusor, ya sea para incorporar cabezales múltiples, o extrusores de otros materiales y texturas.

Por esta razón el carro central está diseñado para aceptar cabezales de distinta longitud.

Mediante rotación, el extrusor utiliza un tornillo dentado para introducir o sacar

El filamento caliente sale por el inyector

La superficie de impresión se mueve por la correcta
posición en los ejes X/Y/Z para dejar el material

El material del extrusor es repartido por el modelo
donde es necesario

### Conformidad

Por medio de la presente Fundació Privada Centre Cim declara que BCN3D+ cumple con los requisitos esenciales y cualesquiera otras disposiciones aplicables o exigibles de las Directivas.

Directiva de Baja Tensión 2006/95/CE Directiva de máquinas 2006/42/CE Directiva RoHS2011/65/UE

### Seguridad

Para evitar posibles riesgos residuales para el usuario, se ruega leer con atenciónlas siguientes medidas de seguridad. REPRAPBCN SE EXIME DE CUALQUIER RESPONSABILIDAD SI EL USUARIO NO RESPETA LAS SIGUIENTES INDICACIONES DE USO:

- Muy importante. Como cualquier electrodoméstico, no tocar los bornes de los cables provenientes de la red eléctrica. La tensión es 230V y existe el riesgo de electrocución. Los demás cables de la máquina trabajan a 12V y no existe riesgo alguno.
- Esta máquina genera y emite radiofrecuencias durante su uso. Es importante instalar y hacer uso del equipo de acuerdo a las instrucciones de este manual para evitar interferencias perjudiciales con electrodomésticos como la televisión o la radio. En caso de que la máquina cause interferencias, aumente la separación entre ésta y los otros electrodomésticos.
- Los materiales de impresión no son inocuos y pueden emitir humos tóxicos. Imprimir siempre en lugares abiertos o con ventilación.
- No respirar a menos de 25cm del cabezal o cabezales extrusores en funcionamiento.
- No situar ningún objeto ni ninguna parte del cuerpo entre las partes móviles de la máquina cuando esté encendida.
- No tocar las partes calientes (hotbed y hotend) cuando la máquina esté encendida, ni durante los 15 minutos posteriores a su funcionamiento.
- No conectar o desconectar ningún dispositivo y/o conector eléctrico con la máquina conectada a la corriente.
- Supervisar el buen funcionamiento de la impresora durante su funcionamiento
- En caso de emergencia, detener la máquina mediante el botón de bloqueo y desconectar la alimentación eléctrica.

Para remarcar la importancia de la seguridad, se han indicado los riesgos mediante etiquetas indicativas, dispuestas en la máquina en las zonas pertinentes.

Señalización de seguridad
Las siguientes señales se han puesto en la impresora para prevenir a los usuarios sobre las áreas de riesgo que pueden entrañar las partes de la máquina o de posibles acciones que no son recomendables para el buen funcionamiento de la impresora 3D.

Peligro superficie caliente.

Partes móviles, peligro de aplastamiento.

Superfície caliente dejar enfriar antes de manipular.

Partes móviles peligro de aplastamiento desconectar antes de manipular.

### 2. PRIMER CONTACTO

### Desembalaje

La BCN3D+ se entrega dentro de una caja de cartón debidamente asegurada, de medidas 600mm largo, 570mm ancho y 590mm alto. Para desempaquetar la BCN3D+ correctamente debemos seguir los siguientes pasos:
1. Retirar la cinta de embalaje superior y abrir las tapas.
2. Retirar la lámina de cartón. Vemos la BCN3D+ y una caja de accesorios fijada en la doble pared de la caja.
3. Cortar las bridas que sujetan la caja de accesorios y retirar dicha caja, la abriremos a continuación.
4. Con cuidado retirar el cartón que forma la doble pared interior de la caja.
5. Si es posible con ayuda, sacar la BCN3D+ de la caja tirando de sus perfiles superiores. Nunca se debe tirar de las guías de los ejes o barras roscadas. Junto con la máquina se extrae la tapa inferior de cartón, unida mediante bridas.
6. Seguidamente cortar las bridas de las patas de la BCN3D+ para retirar la tapa inferior de cartón.
7. Una vez tenemos la máquina fuera de la caja y sin ningún cartón, procedemos a cortar las bridas que inmovilizan sus ejes:
- Bridas que retienen el carro del extrusor
- Bridas que retienen la base calefactada (hotbed)
- Bridas que sujetan el eje Z en su posición más elevada
8. Procedemos a abrir la caja de accesorios. En ella encontramos:
- Vidrio de la base calefactada (hotbed)
- Cable alimentación
- Laca (3DLAC)
- Herramientas
9. Desembalar el vidrio y colocarlo sobre la base calefactada (hotbed). Fijarlo con las pinzas.
10. Sacar el cable de alimentación y conectarlo a un enchufe y a la máquina (esquina posterior izquierda)
11. Sacar la bolsa de herramientas y la laca y dejarlas cerca de la máquina, las utilizaremos a menudo.
12. Colocar la bobina de material suministrado sobre el soporte montado en la parte superior de la BCN3D+.
13. La máquina está lista para montar el hilo de la bobina y cargar los archivos para imprimir.
- Tarjeta SD para cargar nuestros archivos a la impresora
- 2 Bobinas de 1Kg de PLA
- Pieza de olástico de dos colores utilizada para la calibración
- USB con toda la documentación necesaria

Herramientas y accesorios; Útil de calibración; Juego de llaves Allen; Alicates; Destornillador plano; Destornillador; de estrella

La BCN3D+ viene acompañada de un kit de herramientas. En él se incluye todo lo necesario para montar desde cero
la BCN3D+. Además, se incluye un bote de laca (3DLac) diseñado especialmente para su uso en impresión 3D.

El kit consiste en:

Llave boquilla/break 1
Llave Bloc 2

Vista esquerra; Vista frontal; Perspectiva

Diagrama de la BCN3D+

1. Pantalla LCD
2. Ranura tarjeta SD
3. Conector USB
4. Hotbed (base calefactada)
5. Hotend (Extrusor)
6. Guías eje X
7. Varillas roscadas y guías eje Z

8. Guías lineales eje Y
9. Finales de carrera mecánicos (Endstop)
10. Motores paso a paso
11. Toma de corriente
12. Botón de encendido
13. Fuente alimentación
14. Soporte bobina

Extrusor (Hotend); Cabezal; Electrónica; 10. Pololus 11. Arduino + RAMPS

1. Disipador de calor
2. Barrera térmica
3. Bloque calefactor
4. Boquilla (Nozzle)

5. Balancín
6. Tornillo de apriete
7. Ventilador de capa
8. Ventilador Hotend
9. Carro eje X

## ENDSTOP ENDSTOP

x3

### 3. PUESTA EN MARCHA

### Calibración de la altura de la superficie de impresión

Para un correcto funcionamiento, es clave que el plano de movimiento de la boquilla sea perfectamente paralelo a la superficie de impresión.

Y para conseguirlo es necesario calibrar la orientación de la superfície de impresión mediante los 3 tornillos de que dispone.

Con una base mal calibrada NO SE PUEDE IMPRIMIR, y se corre el riesgo que la boquilla (nozzle) choque contra el cristal de la superfície de impresión, o que la primera capa de la impresión no se adhiera bien. Para calibrarla correctamente se deben seguir los siguientes pasos:

1. Hacer Autohome (Prepare/Autohome) para que la máquina mueva los ejes a la posición inicial. La primera vez se debe ir con cuidado pues el nozzle puede colisionar con la base. Si se prevé que esto va a suceder, pulsar manualmente el final de carrera del eje Z.
2. Ajustar el tornillo que acciona el final de carrera, para que el nozzle esté a punto de tocar el cristal al hacer Autohome.
3. Apretar/aflojar los tres tornillos negros que sujetan la base para nivelarla. La distancia entre la boquilla y el vidrio de la base calefactada tiene que ser de 0,2 mm. (Usar un papel doblado para comprobar este margen)
4. Mover el extrusor con la mano hacia el extremo izquierdo (si ofrece resistencia desactivar los motores en Prepare/ DisableSteppers). Nivelar la base con el papel doblado de la misma forma.
5. Mover la base hacia delante para hacer lo mismo en la parte trasera de la base.
6. Repetir este proceso hasta que la base esté nivelada en los cuatro extremos.
2. 3.

x 0

z
y

### Calibración de la distancia relativa

El kit de mejora para Dual Extruder requiere una calibración de la distancia relativa entre las boquillas para garantizar una buena afinación en la unión entre los dos materiales de impresión. El modelo montado fully assembled del dual extruder ya esta calibrada.

Es necesario calibrar cada vez que se desmonte alguno de los BCNozzle. El procedimiento de montaje influye en la posición de las boquillas.

Para proceder a obtener los valores de la distancia relativa entre boquillas ( valores de offset ) serán necesarias 2 archivos, se podrán descargar en nuestra sección de descargas en la web o en la carpeta de calibración, puesta en marcha de la SD ( si se ha comprado el model montado con la upgrade Dual extruder.)

Una vez tengamos los archivos: configuración “Dual_PLA_Slic3r.ini” y la pieza de calibración “Calib.amf”

Abrir el Slic3r (se puede descargar desde nuestra web, apartado de software. Principios básicos en el partado 5 de este manual) y cargar la configuración Dual_PLA_Slic3r.ini y la pieza Calib.amf.

Al cargar una configuración con múltiples extrusores aparece el siguiente mensaje de advertencia:


Slic3r solo carga la configuración del Filament Settings para el primer extrusor. Por ello, conviene crear subconfiguraciones para cada tipo de plástico que se vaya a usar. Clicamos a aceptar i procedemos a cargar la configuraciones del segundo extrusor.

1. Ir a Filament Settings.
2. Hacer las modificaciones pertinentes de los parámetros para el plástico del segundo extrusor.

Estos son los parámetros orientativos para los plásticos más comunes:

ABS
- Temp Extruder: 250ºC
- Temp Bed: 70ºC
- Enable Auto cooling
- Min Fan Speed: 35
- Max Fan Speed: 50
- Bridges Fan Speed: 50
- Disabled Fan for the 2 first layers
- Enable fan if layer print is below 60 seconds
- Slow down if layer print is below 30 seconds
- Min Print Speed: 10 mm/s

PVA
- Temp Extruder: 190ºC
- Temp Bed: 55ºC
- Enable Auto cooling
- Keep Fan always on
- Min Fan Speed: 35
- Max Fan Speed: 100
- Bridges Fan Speed: 100
- Disabled Fan for the 1 first layers
- Enable fan if layer print is below 60 seconds
- Slow down if layer print is below 30 seconds
- Min Print Speed: 10 mm/s
3. Clicar el icono del disquete (save current filament settings). Guardar con el nombre deseado.

PLA
- Temp Extruder: 220ºC
- Temp Bed: 45ºC
- Keep Fan always on
- Enable Auto cooling
- Min Fan Speed: 35
- Max Fan Speed: 100
- Bridges Fan Speed: 100
- Disabled Fan for the 1 first layers
- Enable fan if layer print is below 60 seconds
- Slow down if layer print is below 30 seconds
- Min Print Speed: 10 mm/s

NYLON
- Temp Extruder: 230ºC
- Temp Bed: 0ºC
- Disable Auto cooling

4. En la pestaña Plater, al submenú de la derecha Filament, escoger la subconfiguración creada para cada uno de los extrusores.


5. En función del resultado de la impresión, ajustar offset del extrusor 2: Printer Settings > Extruder 2 > Extruder Offset. En general el error máximo a corregir será de 1mm. A continuación se describe el sentido del ajuste mediante algunos ejemplos para arreglar la desalineación:

Reducir offset en
dirección X y aumentar
offset en dirección Y

Aumentar offset en
dirección X y reducir
offset en dirección Y

Reducir offset en
dirección Y

Aumentar offset en
dirección Y

Aumentar el offset en
dirección X

Reducir el offset en
dirección X

Calibración correcta,
no hace falta
modificar nada

6. Exportar la configuración con los valores del offset retocados: File > Export Config. Exportar G-Code y volver a imprimir la pieza.


7. Volver al paso 5 hasta conseguir el resultado óptimo. Ser riguroso con el resultado. El aspecto de las piezas futuras dependerá de una correcta calibración.

### Carga de filamento

Una de las operaciones más habituales en nuestra BCN3D+ será la carga y descarga de filamento, por varias razones: un cambio de material, un cambio de color, empezar una bobina nueva, realizar una limpieza, realizar mantenimiento etc.

Para realizar este proceso siempre se deben seguir los siguientes pasos:

1. Calentar el extrusor. Poner el hotend a la temperatura de impresión del material a retirar o a cargar. La más alta de las 2.
Para ello no hace falta seleccionar el menú Preheat, aunque sí es aconsejable si se desea imprimir al acabar la carga si no se va a imprimir Menú>Control>Temperatura>Nozzle>220ºC.
2. Desde Prepare>Move axis> 1mm>Extruder, hacer avanzar el tornillo de extrusión (sentido positivo) y extruir unos milímetros de filamento. Éste procedimiento ayudará a prevenir atascos.
3. Desde Prepare>Move axis> 1mm>Extruder, hacer retroceder el tornillo del extrusor (sentido negativo), hasta que libere el extremo del filamento.
4. Una vez con el hilo fuera, cargar el nuevo. Desde Prepare>Move axis> 1mm>Extruder hacer avanzar el tornillo del extrusor para que coja el filamento nuevo. Avanzar el hilo poco a poco, hasta que salga material por el extremo del hotend.
5. Para una correcta alimentación del material,los tornillos del balancín deben tener un apriete mínimo para permitir la alimentación del hilo, incluso ofreciendo una pequeña resistencia al pinzar su entrada con los dedos.
6. Una vez el extrusor empieza a tirar del filamento, volver a apretar los tornillos de modo que ofrezca una buena presión.
7. Con estos pasos tendremos el filamento cargado y listo para imprimir.


### Trabajando con la BCN3D+

A continuación se muestra el diagrama de funcionamiento de la BCN3D+, des del principio al fin. Como se puede comprobar, existen dos caminos posibles que se comentarán en los apartados siguientes:

CAD model; .STL file; SLIC3R utility (G-code generator); SD card; Controller firmware; CAM (Computer Aided Manufacturing) toolchain; SENDER (USB connection)

### 4. CONTROL LCD

La BCN3D+ se puede operar desde su menú LCD. El control se realiza a partir de un único botón que combina dos movimientos: el giro y la pulsación.

- Girar el botón para desplazarse por el menú.
- Pulsar el botón para seleccionar la opción deseada.

Junto al botón de control existe un botón de emergencia de color rojo, que permite detener la máquina en caso de mal funcionamiento. Este botón detiene la máquina, aunque deja la pantalla y los ventiladores activos. Una vez pulsado no se puede recuperar el funcionamiento de la máquina, hasta que la máquina se reinicie automáticamente.

### Pantalla principal

La pantalla principal informa del estado de la máquina en ese momento, y del estado de la impresión en curso.

1. Temperaturas objetivo/real
2. Velocidad del ventilador
3. Velocidad de impresión (Fr)
4. Indicador de altura de impresión (Z)
5. Indicador de tanto por ciento de lectura del programa de impresión (SD)
6. Barra de estado y tiempo transcurrido
7. Mensajes de información

Temperaturas objetivo y real
En la parte superior izquierda pueden visualizarse 4 valores de temperatura. Éstas indican las temperaturas objetivo (arriba), y las temperaturas reales medidas por los termistores (abajo). El lado izquierdo se refiere al extrusor (hotend), mientras que el lado derecho se refiere a la plataforma calefactada (hotbed).

Velocidad del ventilador
En la parte superior derecha, el display indica el tanto por ciento de potencia que está suministrando al ventilador de capa. Un valor de 0% indica apagado, 100% indica máxima velocidad.

Velocidad de impresión (Fr)
En el lado izquierdo a media altura se encuentra la información de velocidad de impresión. Por defecto este valor es 100%, indicando que se está imprimiendo a la velocidad especificada en el programa de impresión que se está ejecutando.

Este valor es modificable en cualquier momento (incluso sin estar imprimiendo). Para ello, girar el botón de control. De esta manera, con un valor de 150% se imprimirá 1,5 veces más rápidamente de lo que se haya estipulado en el programa de impresión.

NOTA: Al variar la velocidad de impresión se modifican todas las velocidades de los motores, de una manera proporcional y directa al valor de velocidad de impresión, y solo se afecta a las velocidades de los motores (ejes X Y Z y extrusor) y no a la temperatura. Por este motivo, se pueden generar problemas de impresión si se incrementa o decrementa la velocidad en gran medida. Se recomienda no variar este valor en más del 50%.

Indicador de altura de impresión (Z)
En la parte derecha se indica la altura actual del cabezal de impresión.
NOTA: Este dato puede ser incorrecto si la impresora se acaba de encender. En ese momento se indicará Z= 0 pero la altura del eje normalmente será diferente a 0 (estará a la altura a la que se haya parado la impresora anteriormente).

Indicador de tanto por ciento de lectura del programa de impresión (SD)
En la parte inferior se indica el tanto por ciento leído del programa. Nótese que este parámetro hace referencia al tanto por ciento de líneas realizadas del programa Gcode, y no al tanto por ciento de realización de la pieza.

Barra de estado y tiempo transcurrido
En la parte inferior derecha hay una barra de estado con la misma información que el parámetro anterior. Encima de dicha barra se encuentra el tiempo transcurrido desde que se dio la orden de empezar a imprimir.

Mensajes de información
En la última línea se mostraran diferentes mensajes informando de los procesos que está llevando a cabo la máquina.

### Pantalla de menú

Para entrar al menú interno de la máquina, pulsar el botón giratorio desde el menú principal.

En este menú se encuentran tres opciones: Prepare, Control y Printfrom SD o No SD (según si la SD ha sido insertada en la ranura).

http://www.reprap-electronics.de/

Menú prepare

El menú Prepare sirve para operar la máquina sin estar imprimiendo. Se encuentran las siguientes opciones:

- DisableSteppers: Esta opción retira la tensión en los motores, facilitando el movimiento manual del hotbed y del cabezal de impresión.
- Autohome: Esta opción posiciona el cabezal de impresión en el origen.

NOTA: Antes de pulsar esta opción, debe asegurarse que nada obstaculiza el movimiento de todos los ejes. Asimismo, es necesario realizar el proceso de calibrado antes de seleccionar esta opción.

- Preheat: Despliega una lista con distintos materiales. Al seleccionar uno de ellos, la máquina se precalienta hasta la temperatura de funcionamiento para dicho material.
- Cooldown: Corta la corriente en las resistencias, y los elementos calefactores dejan de calentar.

NOTA: La máquina se enfría de manera natural, por lo que las partes calientes pueden seguir quemando.

- Move Axis: Este menú está destinado al movimiento de los ejes. Seleccionar en primer lugar la distancia que se quiere mover, y a continuación un eje. Para desplazar el eje, girar el botón de control. Rotar hacia la derecha para avanzar en sentido positivo, rotar a la izquierda para avanzar en sentido negativo.

Main Disable Steppers Auto Home Preheat Cooldown

NOTA: Antes de pulsar esta opción, debe asegurarse que nada obstaculiza el movimiento de todos los ejes. El eje E no se moverá si el extrusor está a más de 150ºC.

Menú control
El menú Control permite modificar los parámetros de la impresora antes y durante la impresión. Son parámetros mucho más específicos, que requieren un conocimiento más profundo de lógica de control.

Print from SD /No SD

Permite acceder a la memoria SD y seleccionar un archivo almacenado para ponerlo a imprimir. Si la tarjeta no está conectada se muestra el texto No SD. En este caso se debe conectar la BCN3D+ a un PC mediante conexión USB (ver apartado Imprimir).

Print from SD | Print from USB


A modo de referencia, a continuación se muestra el diagrama de menús completo:

Prepare Control No Card; Main menu; Main Disable steppers AutoHome Prepare; Cooldown Move Axis; Prepare; Fan Speed Nozzle Bed; Temperature Fan Speed Nozzle Bed; Preheat ABS Settings; Control Nozzle 1 Nozzle 2; Autotemp Min; Max Fact Fan Speed PID-P PID-I PID-D PID-C; Temperature; Control; Vmax-Y Vmax-Z Vmax-E Vtrav-min Vmin Amax-X Amax-X Amax-X Amax-X Aretract Xsteps/nn Ysteps/nn Zsteps/nn Esteps/nn; Motion; Main Temperature Motion; Main; Card Menu; VXY-Jerk; Vmax-X; Move Axis; Bed; Move Move E1 Move E2; Move; Move X: Y: Z:; Move 10 mm Move 1 mm Move 0,1 mm; Preheat PLA Settings; Preheat all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

### 5. ARCHIVOS .STL

El elemento principal para poder imprimir con la BCN3D+ son los archivos de modelos en 3D.

El tipo de archivo más usado para imprimir en 3D es el formato *.STL. Este formato representa las figuras 3D mediante caras planas triangulares. Cuanto más pequeños sean los triángulos, mayor es la resolución y el detalle del modelo 3D.

### Obtención de archivos .STL

Existen tres vías para obtener modelos 3d para imprimir:

1) Diseño propio: El usuario crea sus objetos con un software de modelado 3D. Es una opción interesante si se tienen conocimientos de modelado.
Existe una amplia oferta de programas, algunos de ellos son gratuitos (OpenSCAD, FreeCAD, Blender), mientras que otros requieren licencia comercial (SolidWorks, Rhinoceros, Inventor etc.). En general todos ellos permiten guardar/ exportar los archivos en formato STL.

Preheat PLA Settings Preheat ABS Settings

Laybrick

2) Descarga: Actualmente existen numerosos repositorios o “almacenes” online, donde la comunidad comparte sus modelos 3D con los demás usuarios. A modo de ejemplo se citan los siguientes:
- www.grabcad.com – Repositorio especializado en modelos de ingeniería, diseño y arquitectura. Los modelos 3D no siempre se encuentran en formato STL, sino en el formato del software usado por el usuario que ha creado el modelo.
- www.thingiverse.com – Repositorio creado por la empresa MakerBot, cuenta con una gran cantidad de modelos en formato STL y herramientas de customización de algunos diseños.
- www.rascomras.com – Primer repositorio 3D en español.
3) Digitalizado: Paralelamente al desarrollo de la impresión 3D, la tecnología de escaneado 3D doméstica está evolucionando a gran velocidad. En este sentido, se recomienda visitar la web http://www.123dapp.com/catch de Autodesk. En ella se proporcionan herramientas gratuitas para obtener modelos digitales a partir de imágenes tomadas con cámara fotográfica.
Otros métodos existentes son: software especializados que combinan el uso de proyectores y cámaras, o escáneres 3D.

### Edición y reparación del .STL

Como se ha comentado, un archivo en formato *.STL no siempre se encuentra en buen estado. Algunos errores comunes son:

- Agujeros. El modelo a imprimir debe estar cerrado, sin agujeros.
- Orientación de las caras. Como hemos dicho, un modelo STL se compone de caras planas. La orientación de todas las caras debe ser la misma y hacia afuera de la pieza. En otras palabras, no puede ser que unas caras “miren” en un sentido y otras en otro, todas deben apuntar hacia afuera. Esto sucede de manera accidental al trabajar con los software de modelado.

Existen varios software para editar y reparar archivos STL corruptos. RepRapBCN recomienda Netfabb, que en su versión gratuita BASIC permite realizar las operaciones básicas de edición (escalar, rotar, cortar, combinar, etc.), reparación y medición.

http://www.netfabb.com/downloadcenter.php?basic=1

A continuación se describe la información esencial para la edición de archivos STL en Netfabb. Se recomienda consultar la página oficial para tener un conocimiento más profundo.

### Interfaz de Netfabb

Tras la instalación de Netfabb, es conveniente familiarizarse con su interface. En primer lugar, se habilitará la visualización del volumen de impresión de la BCN3D+. Para ello, clicar en View/Show Platform.

A continuación, se redefinen las dimensiones del volumen. Clicaren Settings/Settings/General/Default PlatformSize. Allí se introducen los valores que corresponden a la BCN3D+: 252 x 200 x 200. Finalmente, clicar en Save.

En la barra de herramientas superior se observan diversos bloques de botones, de los que se destacan:

1) 7 vistas básicas
2) Herramientas de zoom
3) Herramienta de orientar una cara con el plano inferior
4) Herramienta de Mover, Rotar y Escalar
5) Herramienta de reparación

En la parte derecha de la pantalla se dispone la información básica del modelo y la herramienta de corte.

### Reparación

En caso de que la pieza necesite ser reparada, una señal de advertencia aparecerá en la parte inferior derecha de la ventana. Para reparar el modelo, seleccionar el modelo y clicar en la herramienta Repair.

- A continuación, en la ventana de la derecha, clicar en Automatic Repair, y en la ventana emergente seleccionar Default Repair. Clicar en Execute, y para finalizar, clicar en Apply Repair en la ventana de la derecha.
En la ventana emergente, seleccionar la opción Remove old part para eliminar el archivo original con errores. Si el archivo se ha reparado satisfactoriamente la señal de alerta habrá desaparecido.
- En caso de que el error sea que las caras de la figura están invertidas, el modelo se mostrará todo en color rojo. En este caso, el modelo se puede reparar desde Part/InvertPart.


### Orientar y mover a origen

En primer lugar, se necesita orientar correctamente la pieza, generalmente sobre una cara plana. Para ello, el método más sencillo es seleccionar la herramienta de orientar una cara con el plano inferior (align to bottom plane) y hacer doble clic sobre la cara que estará en contacto con la base de la impresora.

A continuación, se debe mover la pieza al origen. Para ello, seleccionar el modelo (figura en color verde) y usar la herramienta Move. En la ventana emergente, clicar en To origin y luego en Translate para finalizar.

Otras ediciones adicionales que se pueden aplicar son cortar la figura o escalarla.
Una vez el modelo está reparado y editado ya se puede guardar. Para ello, ir a Part/ExportPart/as STL y guardar con el nombre deseado.


### Generación del G-CODE

Llegados a este punto, ya se dispone de un modelo 3D listo para imprimir. Sin embargo, es necesario un último paso. Se debe convertir el archivo en formato*.STL a un archivo que la impresora pueda entender para fabricar el modelo. En otras palabras, se debe generar el archivo de Gcode.

El Gcode es un lenguaje informático usado para controlar máquinas de CNC, incluidas la mayoría de impresoras 3D. Se trata, básicamente, de una lista de instrucciones que indican las posiciones y velocidades a las que se debe mover cada uno de los ejes, y las temperaturas del hotend y hotbed.

Existen diversos software para generar un archivo Gcode a partir de un archivo STL. RepRapBCN recomienda el uso de Slic3r, un software open source que, versión a versión, introduce nuevas funcionalidades y mejoras.

http://slic3r.org/download

Igual que otros software para generar GCodes, Slic3r secciona el modelo 3D en capas, que posteriormente se depositarán para generar el diseño en 3D. En cada capa, se establece una diferencia entre los perímetros y el relleno de la pieza. Además, se puede escoger la secuencia de operaciones, velocidad de impresión, número de perímetros, etc. Dado que hay multitud de parámetros, algunos de cierta dificultad de comprensión, se han preparado configuraciones específicas para facilitar el proceso al usuario novel.

### Configuración del Slic3r

Los siguientes perfiles de impresión se han preparado para la BCN3D+ con una boquilla de 0,4mm, teniendo en cuenta el tipo de pieza a imprimir y su uso posterior.
Éstas deben servir como punto de partida y pueden ser mejoradas para ir más deprisa, conseguir un mejor acabado, etc.

Se describen a continuación:

ST: Configuración estándar con altura de capa de 0,2mm para la mayoría de construcciones.

HQ: Configuración estándar de alta calidad con altura de capa de 0,1mm para la mayoría de construcciones.

HS: Configuración pensada para trabajos en los que necesitamos obtener el modelo de una forma rápida, sin perder mucha calidad.

SV: Configuración especial para piezas tipo envase. No hay relleno y la pieza se va fabricando en espiral con una única superficie, mejorando el acabado superficial.

WALL: Configuración especial para piezas con geometrías muy “exóticas”, como las que se generan con el algoritmo Voronoi (con su máximo exponente en el diseñador Dizingof). No tiene relleno, y se baja la temperatura y velocidad para mejorar los voladizos.

STR: Configuración especial para piezas que requieren unos esfuerzos mecánicos importantes. El relleno se realiza en panel de abeja y se disminuye la altura de capa a 0,15mm para mejorar la adhesión entre las capas.

### Uso básico del Slic3r

A continuación se comentan los aspectos esenciales para el uso de Slic3r. Para un conocimiento profundo de la aplicación, se recomienda leer el manual oficial, disponible en la página web del proyecto:

http://manual.slic3r.org/


Definición impresora
La primera vez que se ejecuta Slic3r aparece un asistente de configuración, en el que, paso a paso se debe introducir la siguiente información:
1) Firmware Type: RepRap (Marlin/Sprinter)
2) BedSize: x: 252 y: 200 mm
3) NozzleDiameter: 0.4mm
4) FilamentDiameter: 2.9 mm
5) ExtrusionTemperature: 220ºC
6) BedTemperature: 55ºC

Cargar perfil
Una vez configurado Slic3r, podemos cargar el perfil de impresión adecuado para el tipo de pieza a fabricar. Para ello, ir a File/Load Config… y seleccionar la configuración a cargar.

Añadir archivos
A continuación, añadir los archivos STL previamente editados y reparados. Se pueden arrastrar directamente sobre la plataforma, o clicar en el botón Add…Se pueden añadir tantos archivos diferentes como se quiera.

Además, se puede imprimir más de una copia. Tan solo es necesario marcar el contorno de la pieza a duplicar (o seleccionarla en la lista de la derecha) y clicar el botón + tantas veces como se desee.

Exportar Gcode
Una vez las piezas se han dispuesto en la plataforma y la configuración se ha ajustado, ya se puede exportar el Gcode. Para ello, pulsar el botón ExportGcode… e indicar la ubicación de guardado y un nombre. Se habrá creado un archivo con extensión *.gcode.

### Uso del Slicer para Dual extruder

Slic3r es capaz de generar G-Codes para impresoras con múltiples extrusores. A continuación se describen algunas operaciones básicas que conviene conocer para usar Slic3r con el Dual Extruder:

Creación de archivos .amf

Slic3r usa el tipo de archivo .amf (Additive Manufacturing File Format) para impresiones con múltiples extrusores. A diferencia de los STL permite guardar información sobre materiales. El proceso para crear un .amf es el siguiente:

1. File > Combine multi-material STL files
2. Seleccionar primer STL (se realizará con el extrusor 1)
3. Seleccionar segundo STL (se realizará con el extrusor 2)
4. Click en Cancel
5. Escoger nombre y ubicación donde guardar el archivo *.amf

Cargar el archivo *.amf (como si fuera un *.stl) para realizar la impresión

### Apuntes y consejos de uso

Una de los principales problemas del doble extrusor es el goteo que se produce en el extrusor que está en reposo. Este goteo, no tan solo ensucia la pieza, sino que también vacía el depósito de plástico fundido. Esto provoca que, al volver a imprimir tras un periodo de inactividad, necesite cierto tiempo para que vuelva a extruir de forma continua.

Para minimizar esta problemática, la configuración Dual.ini incorpora un skirt de la misma altura de la pieza. Este skirt funciona tanto como barrera contra el goteo como para purgar. Sin embargo, el skirt solo se realiza con el extrusor 1 (el de la izquierda). Por lo tanto, al crear el archivo *.amf es recomendable estudiar cual de los dos extrusores trabaja menos. Ese debería ser el extrusor 1.

### Uso de Cura para dual extruder

Cura también permite generar G-Codes para impresores de hasta 4 extrusores. Si bien es cierto que Slic3r permite el control sobre más parámetros, Cura resulta más sencillo de utilizar. Lo más importante, sin embargo, es que resuelve buena parte de los problemas derivados del Dual Extruder que Slic3r no consigue solventar.

Incluye la funcionalidad del skirt alrededor de la pieza (llamada Ooze shield), con la particularidad de que se fabrica con ambos extrusores alternados.

Además, tiene la opción Wipe&Prime Tower que permite purgar el extrusor en reposo antes de volver a imprimir. De este modo se consiguen mejores acabados superficiales en la pieza.

Se puede descargar el programa Cura y la configuración para el Dual Extruder desde nuestra web.

1. Configuración de la impresora en Cura

Al instalar Cura se inicia un asistente que permite configurar los parámetros de nuestra impresora.

En caso de ya tener el Cura instalado, se puede añadir otro perfil de impresora. Para ello, ir a Machine --> Machine Settings --> Add New Machine. Así se iniciará el asistente de configuración. Observar que desde este menú también se puede determinar el offset del segundo extrusor:

2. Impresión de piezas en Cura

Cura no necesita trabajar con archivos *.amf. Basta con añadir los dos archivos *.stl.

A continuación, hacer un click en uno de los modelos y seleccionar la opción Dual Extrusion Merge. El modelo amarillo se realizará con el extrusor 1 y el rojo, con el 2


### Transferencia del G-CODE a la BCN3D+

Finalmente, tan solo hace falta transferir el Gcode a la impresora para iniciar la impresión. Para ello, existen dos procedimientos distintos, en función de la comodidad para el usuario y de la disposición de la impresora y el ordenador:

1) Mediante pantalla LCD. Usar una tarjeta SD, cargada con el archivo Gcode a imprimir e introducirla en la ranura lateral de la pantalla de la BCN3D+. Una vez insertada, pulsar el botón de control y escoger la opción Printfrom SD para seleccionar la pieza.
2) Conexión al pc. Usar un software para conectar la impresora al ordenador a través de USB. Desde RepRapBCN recomendamos RepetierHost

http://www.repetier.com/download/

Un software abierto y gratuito que, además, permite visualizar los STL, monitorizar el progreso de impresión y cargar STL, generando automáticamente los Gcodes a través de configuraciones precargadas.

Una alternativa más simple a RepetierHost es el software PrintRun

https://github.com/kliment/Printrun

### 6. IMPRESIÓN DESDE TARJETA SD Y USB

Una vez escogida la pieza que se quiere imprimir, y tras haber calibrado la máquina y comprobado que todo funciona correctamente, se debe proceder de la forma siguiente:

- Asegurarse de tener cargado el material o materiales en la impresora.
- Precalentar la impresora mediante los comandos siguientes de la pantalla LCD:

Menú principal > Prepare > Preheat > Preheat all > PLA (o el material deseado)

- Una vez alcanzada la temperatura de trabajo en el extrusor, hacer un purgado del material:

Menú principal > Prepare > Move axis > 1 mm > Move E1 o 2

Girando la rueda en sentido horario unos pocos milímetros, hasta que salga material de forma continua por la boqui¬lla. Luego retirar el material extruido.

- Insertar la tarjeta SD en lado izquierdo del módulo de la pantalla, prestando atención a la posición de la tarjeta y vigilando de no introducirla por el orificio posterior.
- Iniciar la impresión seleccionando el archivo deseado:

Menú principal > Print from SD > Nombre_archivo

A partir de aquí la impresora empezará la construcción de la figura. Conviene prestar atención al proceso de fabricación, especialmente durante las primeras construcciones.

### Impresión con un solo extrusor

El montaje del Dual Extruder sigue permitiendo la impresión con un solo extrusor.

Para ello, tan solo hace falta cargar una configuración convencional de un solo extrusor. Por defecto, el extrusor que realizará la tarea será el 1 (izquierdo). En caso de querer imprimir con el extrusor 2, tan solo haría falta abrir el G-Code generado (con Bloc de Notas, por ejemplo) y añadir la palabra T1 en las primeras líneas de código, tal y como se describe a continuación:

G21 ; set units to millimeters
M190 S55 ; wait for bed temperature to be reached
M104 S210 T1 ; set temperature
G28 ; home all axes
M109 S210 T1 ; wait for temperature to be reached G90 ; use absolute coordinates
G92 E0
M82 ; use absolute distances for extrusion
T1
G1 F2100.000 E-3.00000 .....

### Qué configuración usar

Tanto para Slic3r como para Cura se han preparado dos configuraciones (las puedes encontrar en nuestra web) para PLA y ABS, los plásticos más comúnmente usados. Dado que cada plástico requiere temperaturas y otros parámetros diferentes estas configuraciones permiten conseguir un mejor acabado superficial.

En caso de combinar diferentes materiales en una misma impresión, usar como base la configuración del plástico más abundante en la pieza. En caso de considerarse oportuno, modificar los parámetros para llegar a un compromiso.

### Superficie de impresión disponible

Con el Dual Extruder montado, el volumen de impresión de la BCN3D+ es de 175 x 190 x 200 mm.

En caso de querer imprimir con un solo extrusor, el volumen es de 200 x 190 x 200 mm.

### 7. FILAMENTOS

La BCN3D+ presenta sus mejores resultados de impresión con PLA, ABS y Nylon, aunque acepta muchos otros materiales, en formato filamento de tipo plástico de 3mm.
A continuación se presenta una breve descripción de los materiales aceptados actualmente:

PLA
El PLA (poliácido láctico) es el material de impresión 3d por excelencia, gracias a su facilidad de conformado mediante FDM. Es el material recomendado para iniciarse en este tipo de tecnología de fabricación. Existe una gran variedad de colores y permite conseguir geometrías complejas sin una gran dificultad. El acabado es ligeramente brillante o semi-mate.

Para la impresión, se trabaja a temperaturas que oscilan entre los 195ºC y los 220ºC, en función del proveedor de material y de la velocidad de impresión. Para la construcción de voladizos se requiere ventilador de capa. Presenta una gran adherencia en la base de cristal, y si se trabaja a una temperatura de cama de 45ºC-55ºC no requiere de ningún producto para garantizar esta adherencia.

Las propiedades mecánicas son medias, aunque presenta una cierta fragilidad en piezas que requieren deformación. A partir de una temperatura de trabajo de unos 50º, las piezas pueden presentar deformación. Se disuelve en sosa cáustica.

ABS
EL ABS (Acrilonitrilo Butadieno Estireno) es otro de los materiales más usados en la impresión 3d, y suple alguna de las flaquezas del PLA. Su impresión es más compleja y requiere de ciertos cuidados. No se recomienda el ABS para usuarios inexpertos. La variedad de colores también es muy alta y el acabado es semi-mate o mate.

El ABS se imprime a temperaturas entre 210ºC y 240ºC en función del proveedor de material y de la velocidad de impresión. El ABS presenta mejor comportamiento que el PLA ante los voladizos, y necesita de menos aire en el ventilador de capa (un exceso de aire puede ser perjudicial). La adherencia en la base es más delicada que en el PLA, debido a la contracción del material al enfriarse, y suele requerir laca adhesiva a pesar de trabajar con una temperatura de hotbed de 70ºC. Si la geometría de la pieza a imprimir presenta una base demasiado grande, se fomenta todavía más el problema de adherencia, debido al gran levantamiento que se produce en los extremos de la pieza (fenómeno conocido como warping. Ver apartado 11 Diagnóstico de la calidad impresión).

Nylon
El Nylon es una poliamida fácilmente imprimible, pero con grandes problemas de adherencia en la base. Es un material ligeramente translúcido y que presenta cierta flexibilidad. El color es blanco, aunque acepta el tintado. Su uso es recomendado para evitar el desgaste en piezas que sufran fricción en su uso habitual.

Se imprime a una temperatura similar a la del PLA, y suele requerir el uso de técnicas alternativas para garantizar la adherencia en la base. El uso de bases especiales (garolite, tufnol) o en su defecto, el forrado de la base de cristal con cinta de carrocero, ayuda a solventar parte del problema del warping. Las piezas con la base demasiado grande no aceptan el uso del nylon. Las propiedades mecánicas son mejores que las del ABS.

### Materiales en fase experimental

HIPS
El HIPS es un material con unas propiedades similares al ABS, pero que reacciona delante de solventes distintos (limoneno). Se suele utilizar como material de soporte para imprimir en ABS.

PVA
El PVA (Polyvinyl alcohol) es un material enfocado únicamente a la fabricación de soportes para la impresión de voladizos. Es soluble en agua, lo que favorece su eliminación de una forma sencilla y segura.

Laybrick
El laybrick es un material en base a plástico que simula el acabado de la piedra. Se extruye con unas características similares al PLA, aunque presenta cierta tendencia a obstruir las boquillas. No se recomienda si no se es usuario experto.

Laywood
El laybrick es otro material en base a plástico que imita el acabado de la madera. No debe ser extruido en boquillas estándar de 0,4 debido al tamaño de sus partículas, que provocan un atasco. Se desaconseja para usuarios no expertos.

Filaflex
El filaflex es un material flexible que se presenta en distintos colores. Su extrusión es sencilla, aunque necesita el uso de una boquilla de 0,6mm.

### 8. FIRMWARE

### ¿Qué es el firmware y cuándo actualizarlo?

El firmware es el software necesario para controlar un hardware. Es decir, es el programa interno que controla la BCN3D+, y permite que desempeñe sus funciones normalmente. La BCN3D+ se entrega ya instalada con la última versión del firmware publicada en la web.

Sus funciones básicas son:

Por un lado, interpretar los archivos .gcode que deseamos imprimir a instrucciones útiles para impresión, pulsos en los drivers para mover motores o temperaturas objetivo.

Por otro lado también se encarga que gestionar los periféricos de la máquina como son la pantalla, para poder interactuar con ella sin necesidad de conectarse a un ordenador, o los finales de carrera, necesarios para el correcto funcionamiento de nuestra impresora.

Normalmente el firmware de un dispositivo viene integrado en éste y no es posible modificarlo o cambiarlo por otro a menos que el fabricante quiera hacerlo y lo haya previsto en su momento.

La ventaja de nuestra impresora RepRap es que sigue la filosofía de Open Source de modo que si queremos podemos cambiar o modificar el firmware para adaptar nuestra máquina a nuevas funcionalidades y accesorios o mejorar su comportamiento.

La posibilidad de modificar el firmware queda bajo la responsabilidad de cada usuario. RepRapBCN siempre desarrollará firmware orientado a la impresión con sus productos, y los difundirá libremente para su uso.

Así pues, fuera de las modificaciones puntuales que cada uno decida hacer en su máquina.

### ¿Cuándo es necesario actualizar el firmware?

Será necesario siempre que cambiemos alguna funcionalidad de nuestra máquina que implique un cambio en su sistema de control. Por ejemplo, un nuevo cabezal extrusor, dual extruder, paste extruder, etc…También es necesario si se cambia cualquier componente de nuestra máquina como tamaño de poleas, finales de carrera, termistores, longitud de ejes, velocidades o aceleraciones de impresión…
Finalmente, se puede cambiar el firmware al recibir una actualización de RepRapBCN. En estos casos se anunciará su publicación vía página web y redes sociales, y sus mejoras y novedades respecto la versión anterior.

### Descargar el IDE de Arduino

En este apartado se indican los pasos a seguir para poder actualizar/modificar el firmware controlador le la impresora.

El primer paso consiste en instalar el IDE de Arduino en un ordenador. Este es el programa que nos permitirá interactuar con la tarjeta Arduino de la BCN3D+.

1. Descargar el paquete de software ARDUINO de la web http://www.reprapbcn.com o abrirlo desde el USB subministrado.

2. Instalar el programa.
3. Una vez instalado, conectar la BCN3D+ al ordenador mediante un cable usb. De esta manera se establece la conexión con el arduino.

La primera vez que se conecta una placa a un ordenador hace falta instalar los drivers del componente. Si el ordenador no instala los drivers automaticamente al conectar la placa, seguir los pasos explicados en:

http://arduino.cc/en/guide/windows#toc3

4. Abrir la aplicación Arduino
5. Desde el menu Archivo>Abrir, seleccionarla versión de firmware guardada
o descargada anteriormente.
El archivo que se debe abrir tiene extensión*.ino, y se encuentran en una carpeta con el mismo nombre, mezclado con todos los subprogramas del firmware.
6. En este momento se pueden modificar los parámetros deseados si es necesario.
7. Seleccionar el modelo de tarjeta Arduino y el puerto desde Herramientas>Tarjeta>Arduino Mega 2560 y Herramientas>Puerto Serial>COM X
- La tarjeta con la que opera la BCN3D+ es una Arduino Mega 2560.
- El puerto se refiere al conector dónde tenemos conectada la placa en el ordenador (Puerto COM). Podemos consultarlo en el sistema operativo (Windows) desde Inicio>Equipo>Boton derecho>Propiedades>Administrador de Dispositivos> Puertos COM y LPT.

8. Seleccionar el boton Cargar.

Emprieza la carga, primero con la compilación del programa para detectar errores, y a continuación con la propia carga en la memoria de la placa.
9. Si el proceso termina correctamente se mostrará el mensaje “Carga terminada”, y la impresora estará lista para utilizar.

### 9. SOLUCIÓN DE PROBLEMAS

### Corrección de histeris y backlash

El efecto de la histéresis es puramente mecánico y derivado del backlash que tienen parte de los componentes usados en nuestras impresoras BCN3D+. En el punto en que la plataforma de impresión debería cambiar de dirección para proseguir con el dibujo de una figura, ésta misma no podía cambiar la dirección hasta pasados unos instantes. Éste efecto es lo que llamamos histéresis. El efecto se producía básicamente en el cambio de dirección en el eje Y. El resultado se podía apreciar sobretodo en la impresión de círculos, donde se producía un alargamiento de la forma justo en los puntos de cambio de eje.
La solución implementada en el firmware permite ‘forzar’ la corrección del eje y o x justo en el momento en que éste cambia de dirección. En el punto de cambio de dirección, se obliga a la plataforma de impresión a corregir su posición bajando o subiendo según en la dirección que se haya producido el cambio. De este modo se arregla el hecho que la plataforma no pueda cambiar de dirección rápidamente (histéresis) y, por lo tanto, desaparece el alargamiento citado anteriormente.

Podemos acceder al menú Histéresis des de:

Menú principal > Control > Motion > Hysteresis

Dentro del menú de histéresis encontramos las opciones:

- Círculos: Nos configura unos valores de corrección estándar para realizar círculos
- Manual x: Permite fijar manualmente la corrección de la histéresis en el eje x
- Manual y: Permite fijar manualmente la corrección de la histéresis en el eje y
- Disable: Desactiva la corrección de la histéresis

Ésta actualización de firmware ya viene con un valor de corrección de histéresis preestablecido para que se puedan empezar a imprimir círculos sin problema.

### Store & Load memory

Función que permite guardar los parámetros fijados en el menú Control en la memoria de la impresora. Estos parámetros guardados se mantienen después del apagado de la impresora.

- Si se quiere guardar la configuración de control

Menú > Control > Store Configuration

- Si se quiere restaurar la configuración previamente guardada

Menú > Control > Load Configuration

Con esta mejora podremos decidir cuál es la configuración de control que mejor se adapta a las características mecánicas de nuestra impresora y guardarla.

### Es difícil sacar la pieza una vez acabada

Una vez acabada una pieza a veces es difícil sacarla:

- Dejar enfriar la base, cuanto más fría está menos adhesión.
- Con la ayuda de un cúter, colocarlo cuidadosamente debajo de la pieza e ir moviéndolo hasta retirarla por completo.
- Es muy recomendable sacar el cristal de la base aflojando los tornillos blancos. Si se intenta sacar la pieza directamente sin sacar el cristal se puede descalibrar y/o forzar los tornillos que ajustan la altura de la base.

### Un motor no gira correctamente (ajuste de pololus)

Desde el menú de la pantalla LCD Prepare/Move Axis, se puede comprobar si los motores funcionan correctamente moviendo los ejes. Se procederá de la siguiente manera:

1. Antes de nada, mover con la mano el eje de los motores para asegurarse que se mueven, y que no hay nada que entorpezca. Si siguen sin moverse bien, ajustar los pololus como se indica a continuación:
2. Si los motores no se mueven o no se mueven lo suficiente,
les falta potencia. Apagar la máquina y girar el potenciómetro del
pololu 5 minutos de reloj en sentido horario.
3. Si los motores se mueven pero en ciertos momentos hacen movimientos bruscos, es decir, pierden pasos, es que tienen demasiada potencia. En ese caso hacer lo mismo pero girando el
potenciómetro 5 minutos en sentido antihorario.

NOTA: Antes de pulsar esta opción, debe asegurarse que nada obstaculiza el movimiento de todos los ejes. El eje E no se moverá si el extrusor está a más de 150ºC.

### Se detiene la extrusión

Se puede deber a diversos motivos:
- El motor no gira debidamente:
1. Ajustar la potencia de los pololus.
2. Comprobar que las tuercas del eje del engranaje grande no aprietan contra el extrusor, si no una contra la otra. Asegurarse que el mecanismo gira fácilmente accionándolo con la mano.
3. Comprobar que los cables eléctricos no tenga desperfectos y estén conectados correctamente.
- El hilo no avanza aunque el motor gire:
1. Asegurarse de que la temperatura sea la correcta según el tipo de plástico.
2. Desmontar el extrusor y limpiar bien los orificios de restos de plástico.
3. Subir la temperatura de la máquina al máximo e intentar extruir con la mano con fuerza para que salga el posible atasco.

5 min.

5 min.

- En la pantalla aparece el texto “Mintemp” o “Maxtemp”:
1. La temperatura del hotend ha salido de la zona en la cual debe trabajar. Asegurarse de que las conexiones estén bien y el cableado no esté deteriorado.
2. Si el problema persiste, quitar el hotend de la máquina y asegurarse que el termistor no esté roto y los cables no se toquen, lo cual provocaría un cortocircuito y una mala lectura de la temperatura.
- El hilo se ha enrollado:
1. Asegurarse que la bobina gira correctamente en el soporte, y que el hilo baja más o menos recto y sin tirones hacia el extrusor. Un hilo enredado puede provocar que se rompa o que la bobina se caiga del soporte.
- El cristal está demasiado cerca de la boquilla al empezar la impresión:
1. Apretar los tornillos de la base o el que acciona el final de carrera del eje Z, para que empiece la impresión un poco más arriba y volver a empezar.
2. Volver a calibrar la base.
- Se ha retirado la SD de su alojamiento:
1. Si se retira la SD de la pantalla, la impresión para y no es posible continuar desde el punto donde se paró.

### La pantalla no responde o no muestra nada

1. Apagar la impresora y volverla a encender.
2. Asegurarse que los cables que alimentan la pantalla estén bien conectados. Los dos cables que vienen de la electrónica deben cruzarse.
3. Cargar de nuevo el firmware desde un pc. Si el firmware está mal cargado la pantalla aparecerá en blanco (ver sección 8 Firmware)

### El carro eje X,Y o Z no se desplazan con fluidez

1. Limpiar las guias.
2. Aflojar los tornillos que sujetan las guias.

### 10. DIAGNÓSTICO DE LA CALIDAD DE IMPRESIÓN

En este apartado se va a hacer una lista de los problemas de calidadde impresión más comunes, y la manera de corregirlos o minimizarlos.
En cualquier caso, es recomendable utilizar las configuraciones de nuestra web (www.reprapbcn.com), ya que han sido testadas y funcionan correctamente con la mayoría de piezas para imprimir en este tipo de impresoras.

### La pieza se separa de la base caliente (WARPING)

A veces la piezas no se adhieren bien al cristal del hotbed durante la impresión. Esto sucede sobre todo imprimiendo con ABS, un material con mucha contracción térmica.

En este caso probar las siguientes soluciones:
1. Limpiar bien el cristal para evitar que el polvo u otras substancias interfieran entre la base y la pieza.
2. Impregnar la superficie de cristal con una capa de laca
3. Subir la temperatura de la base cinco grados centígrados.
4. Calibrar la base de impresión como se explica en el apartado 11 Mantenimiento.
5. Imprimir la primera capa con el hotend más cerca de la base. Para ello, aflojar los tres tornillos de la base un octavo de vuelta, o aflojar el tornillo que acciona del final de carrera del eje Z un quinto de vuelta. Las dos acciones provocarán que la base y el hotend estén 0,1mm más cerca, y la primera capa se adherirá mejor.
6. Hacer que la primera capa eche más material (desde Slic3r, PrintSettings/Advanced/FirstLayer).

### En la primera capa no extruye material en toda la geometría

1. Puede suceder que la primera capa no se adhiera correctamente al cristal, o no deje un flujo constante de hilo plástico (únicamente una línea de gotas) en toda la figura.

El problema es que la máquina no está calibrada correctamente; el extrusor está demasiado lejos de la base. Revisar el calibrado del apartado 11 Mantenimiento centrándose en el tornillo de regulación del final de carrera del eje Z.

2. La primera capa presenta uno de los síntomas anteriores solo en una zona de la figura.
La causa es que la impresora no está calibrada correctamente. El eje X y la base no son paralelos y esto provoca que el extrusor se aleje o se acerque demasiado a la base en algunos puntos. Revisar el proceso de calibrado del apartado 11 Mantenimiento, centrándose en la orientación del plano de la base de impresión.

### Aparecen grietas en mitad de la pieza

Esto sucede porque la parte de la pieza más cercana al extrusor está más caliente
que las capas inferiores. Si a esto se le suma que el plástico del perímetro se refrigera antes que la parte interior, se generan unas contracciones internas que pueden llegar a separar las capas de la pieza.

Para evitar estas grietas se debe subir 5 grados la temperatura de extrusión, de manera que las capas se adhieran con más fuerza.

### Fused

Al estar trabajando con material fundido, la gravedad hace que éste tienda a gotear desde la boquilla. Se deberán buscar estrategias para minimizar esta problemática, y conseguir mejores acabados superficiales, incluso con geometrías complejas.

### Deposition

El hilo de material que se extruye tiene el diámetro del orificio exterior de la boquilla del hotend. Mediante la deposición del hilo de ese material se debe cubrir, capa por capa, toda la superficie de la pieza a fabricar. Cabe destacar que el proceso de fabricación se produce de modo secuencial, lo cual permite diferenciar entre diversas partes de cada modelo (como por ejemplo, perímetros y relleno) y escoger entre diversas estrategias de impresión (orden, porcentaje y entramado del relleno, etc).

### Aparecen hilillos de plástico alrededor de la pieza

Esto sucede cuando el extrusor se desplaza de un punto a otro sin depositar material.

Para evitarlo, ajustar la opción retract desde Slicer. Esta opción retira parte del hilo del motor del extrusor, de manera que se disminuye la presión del material en el interior del extrusor y se evita el goteo durante el desplazamiento de los ejes. Si se aumenta el retract, se disminuyen los residuos en forma de hilos.

### Modeling

Al ir subiendo en altura, el material imprimido necesita tener un apoyo. Son muchas las piezas que contienen partes suspendidas en el aire (voladizos) o zonas con mucha inclinación, y el material depositado tiene tendencia a desprenderse hasta enfriarse.

Cuando esto ocurra, se recomienda investigar la creación de columnas de apoyo desde el software de impresión (Slic3r).

### Una capa aparece desplazada respecto a la inferior

Cuando en una pieza existe un desfase de posición entre una capa y las siguientes, lo más seguro es que uno de los motores haya perdido pasos. Primero se debe identificar cuál de los ejes se ve afectado, y después ajustar el pololu correspondiente a ese motor, tal y como se explica en el apartado 9 Solución de problemas.


### 11. MANTENIMIENTO

Dadas las características de la máquina, es muy importante realizar comprobaciones periódicas de las distintas partes, a fin de no perder calidad de impresión y evitar errores.

### Calibración


La BCN3D+ se comercializa montada y calibrada, pero es posible que con el tiempo requiera una recalibrado de sus ejes.
El proceso es sencillo si se siguen los pasos siguientes:
- Calibración eje X
a) Con el útil de calibración, medir la altura de las barras del eje X, desde las chapas de aluminio de la base
b) Ajustar la altura a ambos extremos del eje para garantizar su horizontalidad. Para ello girar manualmente cada barra roscada para ajustar la altura.
- Calibración eje Z

Con el fin de garantizar la perpendicularidad del eje Z con la base, se debe realizar un proceso iterativo que consiste en los siguientes pasos:
a) Colocar el eje Z en una posición vertical (180 mm aproximadamente).
b) Aflojar los tornillos de la base de las guías del eje Z. Con ello se consigueun margen de movimiento que nos permitirá posicionarlos correctamente.
c) Usar el útil de calibración a modo de escuadra. Apoyar su lado corto sobre las chapas de la base de la impresora, y el lado más largo en contacto con las guías verticales del eje Z.
d) Orientar el útil de modo que permita hacer 2 mediciones a 90º y realizar esta operación en ambas guías Z.

e) Durante las mediciones, ir ajustando la perpendicularidad de las guías con el útil, e ir apretando los tornillos de la base para fijar su posición. Como se ha comentado, éste es un proceso iterativo, de modo que una vez se ha aplicado en ambas guías, se debe repetir y corregir posibles desajustes.

### Lubricación de las varillas

Se recomienda engrasar las varillas cada cierto tiempo, en especial cuando no se mueven con facilidad o hacen más ruido de lo normal. Para ello se puede usar cualquier tipo de grasa. Colocar unas gotas por las varillas, y mover los ejes para que el mismo mecanismo las reparta por toda su extensión.
Tambien es necesario poner unas gotas más de grasa por las 2 varillas roscada del eje Z

### Mantenimiento del filamento

Las bobinas de filamento se deben guardar en un lugar fresco y seco. El calor y la humedad afectan bastante a este tipo de plásticos. Si una bobina no se va a usar durante un largo período de tiempo, guardarla en una bolsa de plástico sellada.

Debe asegurarse que el plástico esté bien enrollado. Una bobina con el plástico suelto puede provocar que éste se enrolle mal, y al imprimir provoque tirones que afectan a la impresión y los componentes de la máquina.

### Limpieza de la base de impresión

Después de varias impresiones, el cristal del hotbed se ensucia, y se acumulan capas de laca, polvo y restos de plástico.

Para limpiar el cristal se debe retirar de la impresora. Los restos de laca y polvo se quitan fácilmente poniendo el cristal debajo del agua con un poco de jabón. Si hay restos de plástico enganchados, se pueden retirar con un cúter con cuidado de no rallar el cristal. También se puede usar acetona, ya que diluye el plástico.

### Mantenimiento del Hotend

Si se requiere demontar el hotend para canviar la boquilla o alguna otra de sus partes se puede realizar facilmente siguiendo estos pasos:

- Desmontado del Hotend
1. Sacar el hilo de dentro del hotend siguiendo procedimiento ya explicado en el apartado 3. “Primer contacto con la maquina” en “Carga de filamento”.
2. Enfriar hotend durante unos 15 minutos con la opción Prepare > Cooldown .
3. Hacer Autohome y subir el eje Z hasta +150.00 mm
4. Apagar la alimentación de la máquina
5. Sacar el dos tornillos M3 del Layer fan ring.
6. Desconectar el conector del ventilador y sacar la sujeción del cooler fan del Heat sink.
7. Desconectar el conector de los cables Hotend y cortar las bridas para liberar los cables.

8. Desenroscar el conjunto ‘Heat break+ bloc+ boquilla’ del Heat sink introduciendo la llave bloc al Heat break ,vigilar que los cables no se enreden y se descrimpen. [View 3]
9. Con el conjunto ‘Heat break+ bloc+ boquilla’ fuera , desenroscar boquilla del bloque con la llave bloc y la llave boquilla. Vigilando donde pones la llave para no romper los cables. [View 5]
10. Desenroscar Heat break del bloque con la llave bloc y la llave Heat break. [View 7]
11. Comprobar que todos los componentes estén limpios, si no, limpiarlos cómo se describe más adelante.


- Montaje del Hotend
1. Partimos del bloque (con resistencia cerámica y termistor instalados), boquilla y Heat break por separado.
2. Atornillar la boquilla al bloque con la mano hasta que se tope con el bloque.
3. Una vez atornillado, aflojar un cuarto de vuelta.
4. Atornillar con la mano el Heat break al bloque hasta que tope con la boquilla.
5. Apretar fuerte la boquilla con la llave boquilla aguantando el bloque con la llave bloc. [view 6]
6. Atornillar el conjunto a mano al Heat sink montado a la máquina.


Si los cables quedaran en una posición demasiado forzada, habría que desmontar el mecanismo del extrusor y desenroscar el tres tornillos del Heatsink y girar el Hotend.

7. Apretar suavemente desde el Heat break con la llave break el conjunto contra el Heat sink de la maquina. [view 9]
8. Conectar los cables del hotend.
9. Calentar el extrusor a 220ºC.
10. Volver a apretar, ahora en caliente, la boquilla contra el bloque mediante la llave boquilla y la llave bloque. [view 10]

11. Montar cooler fan al Heat sink y conectar los cables.
12. Montar Layer fan ring con el dos tornillos M3.
13. Embridar cables hotend y del ventilador.
14. Poner en marcha la máquina y comprobar que todas las conexiones funcionan correctamente.
15. Cargar el filamento y extruir plástico.

Necesario:
- Llave boquilla / Llave break (8,2 mm/4,6 mm)
- Llave bloc (20,5 mm)

### Limpiar las partes del Hotend

Para limpiar restos de plástico, u otros restos de material de dentro de las partes del hotend se puede proceder de varias formas;

1. Si los residuos de plástico son de ABS o PLA, sumergir la parte en acetona y dejar toda la noche a remojo. Eliminar los restos con un trozo de alambre que no arañe las partes.
2. Si los residuos están entre los dientes de la rosca del Heat bloc será necesario conectar los cables y calentar el bloque ( 150-220ºC ) y realizar el montaje anteriormente descrito en caliente, extremado las precauciones para no quemarse. Los alicates y las llaves resisten el calor.

LAS REFERENCIAS ‘VIEWS’ HACEN REFERENCIA AL MANUAL 8 Y 9 DE LA WEB.

### 12. CONSEJOS Y ADVERTENCIAS

Hay ciertos aspectos que creemos hay que tener en cuenta a la hora de utilizar y realizar el mantenimiento de la máquina:

- No verter líquidos sobre el hotbed o hotend ya que podrían dañar el resto de componentes. Para hacer limpieza de ambos, primero extraerlos de la máquina. Lo único que se recomienda utilizar con la base montada es la laca para una buena adherencia de las piezas.
- Si cuesta retirar las piezas, hacerlo con la base de cristal fuera de la máquina para evitar descalibrarla.
- No sobrecalentar el hotend. Aunque su temperatura está limitada desde el firmware, no utilizar otros métodos para calentarlo por encima de esa temperatura.
- No manipular las partes electrónicas de la máquina cuando está encendida, podría provocar daños en sus componentes.
- No apagar la impresora inmediatamente después de una impresión. Dejar pasar un tiempo para que los ventiladores enfríen sus componentes.

### 13. ASISTENCIA TÉCNICA RepRapBCN

Si no encuentra en este manual una solución a su problema, puede contactar con el equipo de RepRapBCN mediante los siguientes canales:

### Asistencia SAT

Llama al teléfono de nuestro Servicio de Asistencia Técnica: 93 473 88 24.

### Foro

Antes de proceder a cualquier otra acción, se recomienda consultar nuestro foro. Es muy probable otro usuario haya sufrido el mismo problema, y es en el foro dónde se solucionan la mayoría de ellos.

http://www.reprapbcn.com/es/forum

### Correo electrónico

Si el problema no se soluciona, puede comunicarse directamente con nosotros por correo electrónico. Un experto de RepRapBCN buscará una solución lo más rápido posible.

info@reprapbcn.com

### Teléfono

Disponemos de un teléfono de contacto para preguntar directamente a nuestro equipo, o para concertar una cita para traer la impresora hacer una revisión: 93 348 70 25.

Toda esta información se encuentra disponible en nuestra página web, apartado contacto:

http://www.reprapbcn.com/es/contact

En cualquiera de los casos es importante adjuntar el número de serie de la impresora, para tener un registro y saber de antemano los problemas que surjan. También ayuda una fotografía para identificar más fácilmente lo ocurrido.

### 14. GLOSARIO

- Arduino. Plataforma de hardware libre, basadaen una placa con un microcontrolador y un entorno de desarrollo. Es una placa muy popular, y constituye el “cerebro” de la electrónica de la BCN3D+. Necesita que se le cargue el firmware para trabajar.

http://www.arduino.cc/

- Endstop. Final de carrera. Es el componente electro-mecánico que hace contacto con los carros de los ejes, para indicar el recorrido total de estos.

- Filamento. Bobina de cualquier material válido para imprimir.
- Firmware. Código interno de la BCN3D+ que gobierna toda su electrónica y permite la impresión. La BCN3D+ usa su propio firmware, basado en el popular Marlin.
- Fuente de alimentación. Dispositivo que recibe corriente de la red eléctrica y la adapta a las necesidades de la impresora.
- Gcode. Los archivos en formato Gcode contienen el programa de impresión de las figuras. Se cargan en la memoria SD para que la BCN3D+ los pueda leer e imprimir.
- Hotbed. Base calefactada sobre la que se imprimen los modelos.
- Hotend. Extrusor es la parte donde se aporta calor al filamento para derretirlo y poder imprimir.
- Memoria SD. Tarjeta donde se almacenan los archivos en formato Gcode para imprimir.
- Nettfab. Software recomendado por RepRapBCN para editar y reparar archivos STL.

http://www.netfabb.com/downloadcenter.php?basic=1

- Nozzle. Punta del extrusor, salida del material fundido.
- Open Source. Software distribuido y desarrollado libremente. Se focaliza más en los beneficios prácticos (acceso al código fuente) que en cuestiones éticas o de libertad que tanto se destacan en el software libre.
- Pololu. Componente electrónico que regula el buen funcionamiento de los motores de la impresora.
- RepetierHost. Software que permite enviar los archivos Gcode directamente desde el pc a la máquina, mediante un cable USB. Tiene otras funcionalidades, como monitorizar la impresión.

http://www.repetier.com/

- RAMPS 1.4. Su nombre es el acrónimo de RepRapArduino Mega PololuShield. Es una placa electrónica diseñada especialmente para complementar el circuito de la impresora. Contiene unos fusibles para evitar la destrucción de la placa Arduino en caso de sobrealimentación.
- Slicer. Software recomendado por RepRapBCN para generar archivos Gcode a partir de archivos STL.

http://slic3r.org/

- Termistores. Sensores de temperatura. Encontramos uno en el hotbed y otro en el hotend.
- Ventilador de capa. Ventilador situado justo en la salida del material fundido. Permite enfriar el material en su salida, para igualar su temperatura a la temperatura del material ya imprimido.

### 15. GARANTÍA, DEVOLUCIONES Y POLÍTICA DE SUSTITUCIÓN

Los productos de RepRapBCN no tienen garantía de largo plazo. Todos los componentes de la BCN3D+ tienen un año de garantía. Solo se aceptan devoluciones en productos no afectados, dentro de un plazo de 14 días hábiles después de su recepción. Una vez finalizado ese plazo, todas las ventas se considerarán definitivas. Por productos “no afectados” se entiende que el dispositivo no ha sido nunca montado, encendido, programado o de otra forma alterado. RepRapBCN no puede aceptar devoluciones en artículos adquiridos a los cuales se les ha aplicado corriente eléctrica, o han sido de alguna manera programados, modificados o afectados. Sin embargo, ofrecemos piezas de repuesto o servicio técnico sobres los artículos sobre los que se haya probado que contienen defecto de fábrica, y siempre trabajaremos con usted para volver a poner su equipo en funcionamiento.

### 16. TÉRMINOS Y CONDICIONES DE SERVICIO

Toda la información contenida en este manual está sujeta a cambios sin aviso, y se ofrece para fines meramente de conveniencia para el usuario. RepRapBCN se reserva el derecho de modificar o revisar el manual en cualquier momento a su entero criterio. Usted acepta estar sujeto a cualquier modificación y/o revisión. Póngase en contacto con el equipo técnico de RepRapBCN si desea obtener información actualizada.

El diseño de ese manual y todo el texto, los gráficos, la información, el contenido y demás materiales están protegidos por derechos de autor y otras leyes. Ciertas marcas registradas, nombres comerciales, marcas de servicio y logotipos (las “Marcas”) utilizados son marcas registradas y no registradas, nombres comerciales y marcas de servicio de RepRapBCN y sus socios. Ninguna declaración en este manual confiere ni se entenderá como que confiere, por inferencia, impedimento o de otra forma, ninguna licencia ni derecho de usar ninguna Marca sin el permiso por escrito de RepRapBCN. Cualquier uso no autorizado de la información, los materiales o las Marcas podría violar las leyes de derechos de autor, de marcas registradas, de privacidad y publicidad y/u otras leyes y reglamentaciones.

## Fundació CIM-UPC

### 12, Llorenç i Artigas 08028 Barcelona

T. 934 017 171
F. 934 017 170

### info@reprapbcn.com www.reprapbcn.com

RepRapBCN 2014, All Rights Reserved

## BCN3D+ Dual extruder

## User manual

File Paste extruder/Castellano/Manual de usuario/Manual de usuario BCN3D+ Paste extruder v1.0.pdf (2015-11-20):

User Manual | RepRapBCN

Paste extruder

### 1. INFORMACIÓN PREVIA

Especificaciones
Tecnología PLD
Conformidad
Seguridad

### 2. PRIMER CONTACTO

Contenido de la caja
Diagrama del Paste Extruder

### 3. PRIMER CONTACTO

Montaje del Paste Extruder Carga del firmware
Calibración del eje Z
Carga de la jeringa

### 4. MATERIALES Y EJEMPLOS DE FUNCIONAMIENTO

Puré de patatas
Chocolate
Áridos

### 5. RESOLUCIÓN DE PROBLEMAS 6. MANTENIMIENTO 7. CONSEJOS Y ADVERTENCIAS 8. ASISTENCIA TÉCNICA RepRapBCN 9. GARANTÍA, DEVOLUCIONES Y POLÍTICA DE SUSTITUCIÓN 10. TÉRMINOS Y CONDICIONES DE SERVICIO

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
# INDICE

### 1. INFORMACIÓN PREVIA

### Especificaciones

Tecnología de fabricación:

Dimensiones generales:
Peso:
Volumen de impresión:

Número de extrusores:

Altura de capa:

Temperatura funcionamiento: Volumen de jeringa:

Material admisible

Firmware:

Material Extrusion Fused Filament Fabrication (FFF)

480mm x 480mm x 455mm
1.1 kg
Base: 220mm x 200 mm
Altura: 90mm

1

0,5-1,7mm (con boquilla estándar de 0,4mm) 1-3,5mm (con boquilla de 0,6mm)

15-35 ºC
100mL

Cualquier pasta o líquido con temperatura y viscosidad adecuada

Específico BCN3DPasteExtruder (basado en Marlin)

### Tecnología DLP

Paste Extruder es un extrusor de pastas basado en la tecnología PDL (Paste DepositionLayer).Esta tecnología permite fabricar piezas por medio de la deposición de material a través de una jeringa. Se extruye el material empujando un émbolo con un motor paso a paso a través de un tren de engranajes reductor. Se parte de un modelo digital que se secciona en capas con un software de laminado digital. El cabezal realiza los movimientos necesarios para depositar el material de una capa, luego realiza un desplazamiento vertical y empieza la siguiente capa. El proceso se repite hasta realizar la pieza completa.


La máquina está preparada para incorporar los complementos que publique RepRapBCN, mediante un proceso sencillo y pautado. Uno de los complementos principales es el cambio de cabezal extrusor, ya sea para incorporar cabezales múltiples, o extrusores de otros materiales y texturas.

Por esta razón el carro central está diseñado para aceptar cabezales de distinta longitud.

### Conformidad

Por medio de la presente Fundación Privada Centre Cim declara que Paste Extruder cumple con los requisitos esenciales y cualesquiera otras disposiciones aplicables o exigibles de las Directivas.

Directiva de Baja Tensión 2006/95/CE Directiva de máquinas 2006/42/CE Directiva RoHS2011/65/UE

### Seguridad

Para evitar posibles riesgos residuales para el usuario, se ruega leer con atenciónlas siguientes medidas de seguridad.

REPRAPBCN SE EXIME DE CUALQUIER RESPONSABILIDAD SI EL USUARIO NO RESPETA LASSIGUIENTES INDICACIONES DE USO:

- Muy importante. Como cualquier electrodoméstico, no tocar los bornes de los cables provenientes de la red eléctrica. La tensión es 230V y existe el riesgo de electrocución. Los demás cables de la máquina trabajan a 12V y no existe riesgo alguno.
- Esta máquina genera y emite radiofrecuencias durante su uso. Es importante instalar y hacer uso del equipo de acuerdo a las instrucciones de este manual para evitar interferencias perjudiciales con electrodomésticos como la televisión o la radio. En caso de que la máquina cause interferencias, aumente la separación entre ésta y los otros electrodomésticos.
- Los alimentos impresos con Paste Extruder, son meramente decorativos. No ingerir.
- Seguir la normativa de seguridad del material específico a extruir.
- No situar ningún objeto ni ninguna parte del cuerpo entre las partes móviles de la máquina cuando esté encendida.
- No tocar las partes calientes (hotbed) cuando la máquina esté encendida, ni durante los 15 minutos posteriores a su funcionamiento.
- No conectar o desconectar ningún dispositivo y/o conector eléctrico con la máquina conectada a la corriente.
- Supervisar el buen funcionamiento de la impresora durante su funcionamiento
- En caso de emergencia, detener la máquina mediante el botón de bloqueo y desconectar la alimentación eléctrica.

Para remarcar la importancia de la seguridad, se han indicado los riesgos mediante etiquetas indicativas, dispuestas en la máquina en las zonas pertinentes.

Señalización de seguridad
Las siguientes señales se han puesto en la impresora para prevenir a los usuarios sobre las áreas de riesgo que pueden entrañar las partes de la máquina o de posibles acciones que no son recomendables para el buen funcionamiento del Paste Extruder.

Peligro superficie caliente.

Partes móviles, peligro de aplastamiento.

Superfície caliente dejar enfriar antes de manipular.

Partes móviles peligro de aplastamiento desconectar antes de manipular.

### 2. DESEMBALAJE

### Contenido de la caja

El Kit del Paste Extruder se entrega dentro de una caja de cartón debidamente asegurada, de medidas 260mm largo, 165mm ancho y 105mm alto.
Procedemos a abrir la caja. En ella encontramos:

DESEMBALAJE

- Piezas impresas
- Chapas metálicas cortadas
- Varillas y guías
- Motor NEMA 17
- Tornillería
- Rodamientos y cojinetes
- Jeringa de alimentación 100 ml.


### Diagrama de la BCN3D+ Paste extruder

1. Paste Extruder
2. Vértice adaptado Paste Extruder (*)
3. Adaptación final de carrera eje Z
4. Varilla 140 mm.

*Descargable desde www.reprapbcn.com en formato STL

2.

3.

4.

1.

Vista esquerra | Vista frontal

### Perspectiva


Extrusor

1. Cuerpo del extrusor
2. Pestillo de palanca
3. Embolo dentado
4. Soporte barras guía
5. Tirantes
6. Soportes de los tirantes
7. Tren de engranajes
8. Motor paso a paso
9. Jeringa 100 ml
Abierto | Cerrado


### Final de carrera eje Z

1. Varilla roscada 140 mm
2. Adaptador final de carrera eje Z
3. Final de carrera

### Final de carrera eje X

1. Final de carrera
2. Adaptador final de carrera eje X
3. Carro

### 3. PRIMER CONTACTO

1. Montaje del Paste Extruder (Descargable desde la sección Docs de www.reprapbcn.com)
2. Carga del Firmware (Explicado en el manual de montaje.
Si la carga ha sido exitosa se debería visualizar esta pantalla al encender la BCN3d+.

A continuación se muestra el diagrama de menús completo:

RepRapBCN Hot Bed
Paste
Extruder

0o
25o | 1%
SD | --: -- Ready!
0%
FR 100% | Z:⁺000.0

Prepare Control; No Card/Print from SD; Main menu; Main Disable steppers; AutoHome Preheat Bed Cooldown Move Axis; Prepare; Control Bed; Autotemp; Min Max Fact PID-P; PID-I PID-D PID-C; Temperature; Control; Ve-Jerk Hystrsis; Motion; Main Temperature Motion; Store Memory; Load Memory; Restore Failsafe; Main; Card Menu; VXY-Jerk; Vz-Jerk; Vmax-X; Move Axis; Move; Move X Y Z Extrude; Move 10 mm Move 1 mm; Move 0,1 mm; Circles

Vmax-Y

Vmax-E

Vmax-Z

Vmin Vtrav-min

Amax-Y

Amax-X

Amax-E
Aretract

Amax-Z

Ysteps/mm

Xsteps/mm

Esteps/mm

Zsteps/mm

Manual Y:

Manual X: +000.00
⁺000.20
Disable

3. Calibración del eje Z

El Paste Extruder requiere una calibración de la altura debido a la diferencia de dimensiones en el eje Z con respecto al extrusor normal.

Es necesario calibrar cada vez que se cambie el modelo de jeringa o de boquilla.

- Primero se nivela la cama en caso de que no lo estuviera. Aun en el caso de que se tuviese nivelada deberíamos comprobar que no la hemos desnivelado durante el proceso de montaje del Paste Extruder.
- Se monta la jeringa con el Paste Extruder cerrado tal y como se describe en el manual de montaje. En la pantalla se accede a PREPARE> AUTOHOME, se ajusta a mano la altura de la varilla del final de carrera Z y se repite el autohome. Se repite este proceso hasta lograr una altura de 0,2mm entre la boquilla y la superficie de impresión (se puede medir fácilmente con un folio doblado una vez).
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

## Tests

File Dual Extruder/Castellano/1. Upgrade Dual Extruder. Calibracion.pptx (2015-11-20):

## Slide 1

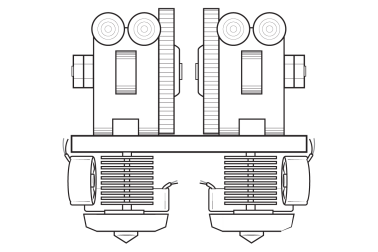
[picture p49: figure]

Upgrade Dual Extruder. Calibración.

Equipo BCN3D Technologies

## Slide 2

CONCEPTOS INICIALES

Antes de explicar el procedimiento de calibración del doble extrusor es importante presentar dos conceptos importantes que se explican en las siguientes diapositivas. Estos son:
- Z OFFSET
- XY OFFSET

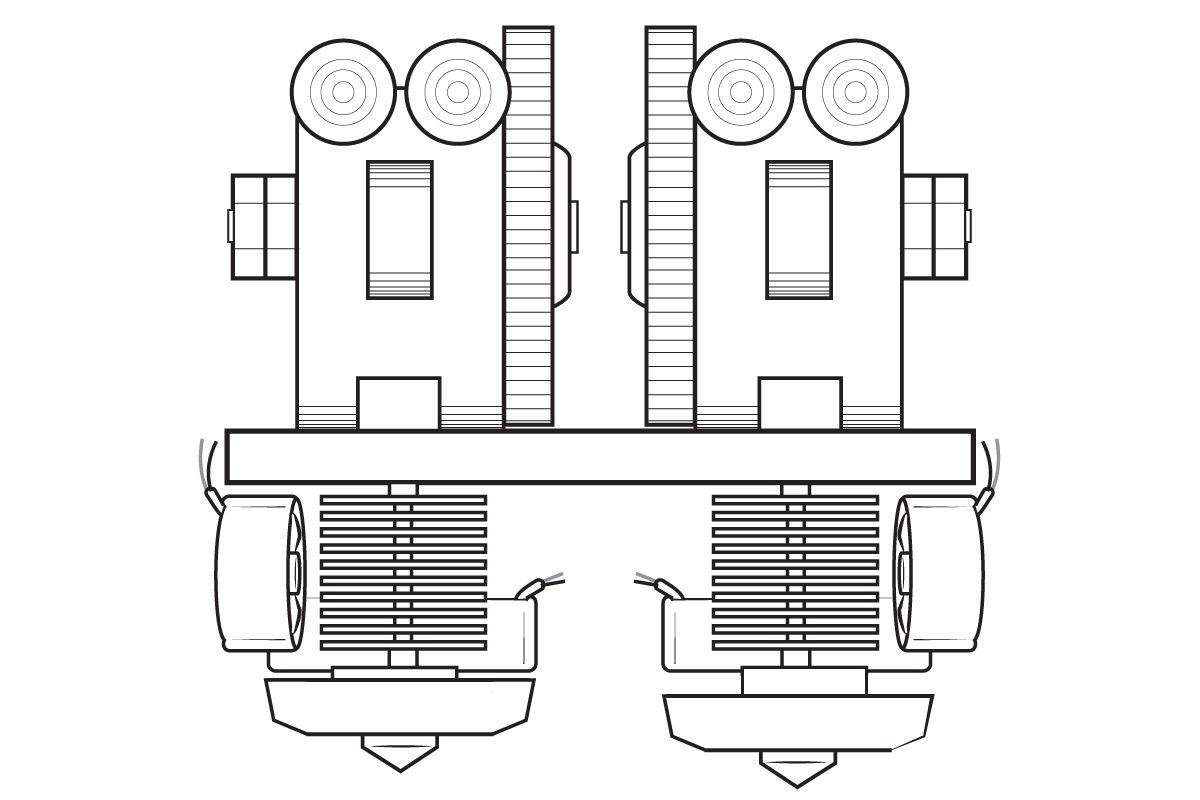
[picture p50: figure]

Extrusor 1

Extrusor 2

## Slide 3

Z OFFSET

¿Qué es el Z offset?

- El Z offset es la distancia Z entre la boquilla de cada extrusor. Las dos deberán estar a la misma altura. La arandela elástica Clover Dome que posee el segundo extrusor será la encargada de ajustar esta distancia.

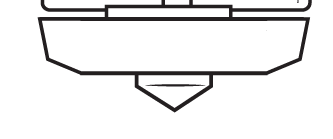
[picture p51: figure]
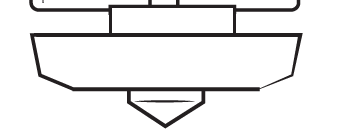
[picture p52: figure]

Z offset

Extrusor 1

Extrusor 2

Vista frontal

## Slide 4

XY OFFSET

¿Qué es el XY offset?

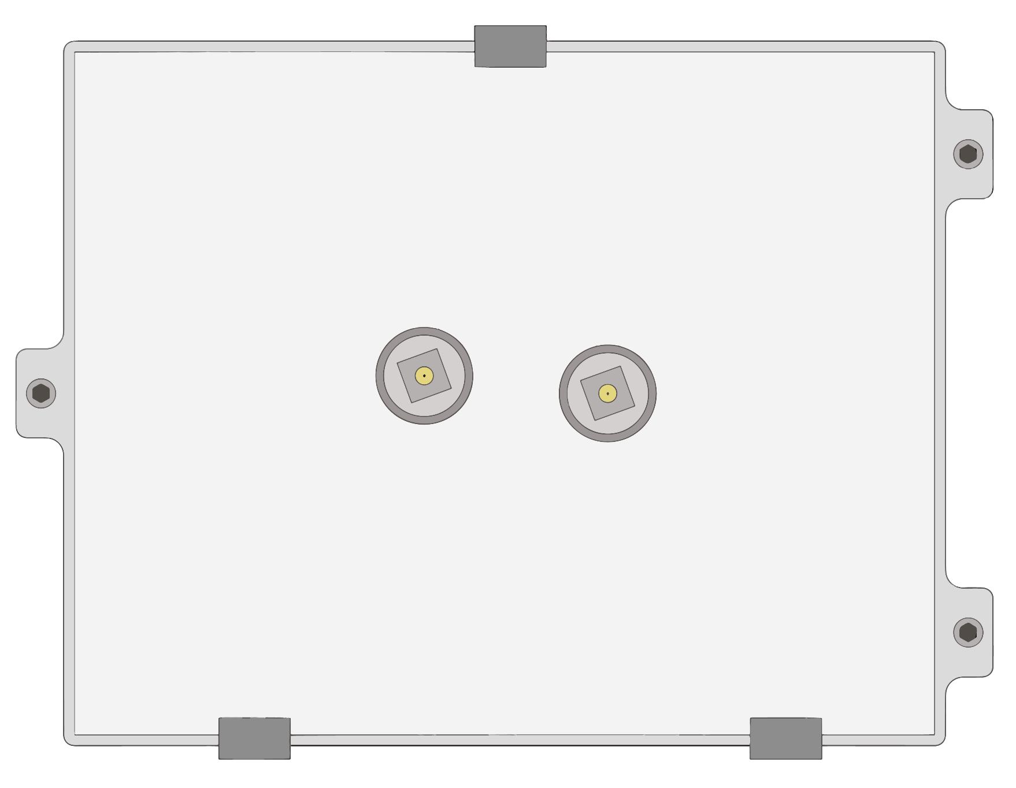
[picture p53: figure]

X offset

Y offset

Extrusor 1

Extrusor 2

Vista inferior

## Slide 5

PROCEDIMIENTO DE CALIBRACIÓN

Una vez conocidos estos dos conceptos, el procedimiento a seguir para la calibración del doble extrusor es la siguiente:
1. Calibrar el extrusor 1
2. Calibrar el extrusor 2
3. Acabar el montaje
4. Encontrar el XY offset

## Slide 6

1. CALIBRACIÓN EXTRUSOR 1

El primer extrusor se debe calibrar durante el montaje del upgrade Dual Extruder. En concreto, en el momento que se monta el carro en las barras lisas. Esto es debido a que de esta manera será más cómoda la calibración del segundo extrusor con los tornillos reguladores de la arandela elástica a la vista.

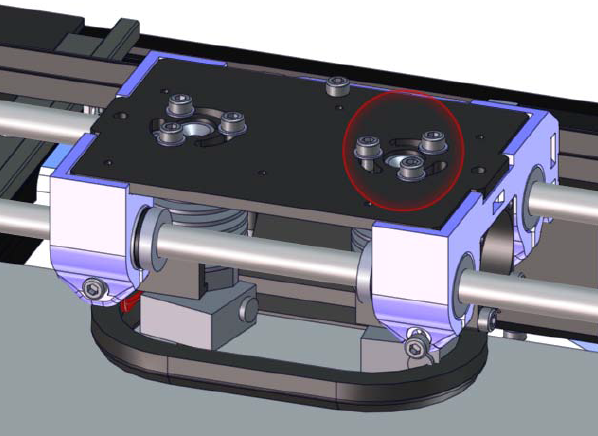
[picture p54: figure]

Extrusor 1

Extrusor 2

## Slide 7

1. CALIBRACIÓN EXTRUSOR 1

Lo primero que se debe hacer es apretar los 3 tornillos del extrusor que lleva la arandela elástica Clover Dome (Ext 2).

Arandela elástica

Ext 1

Ext 2

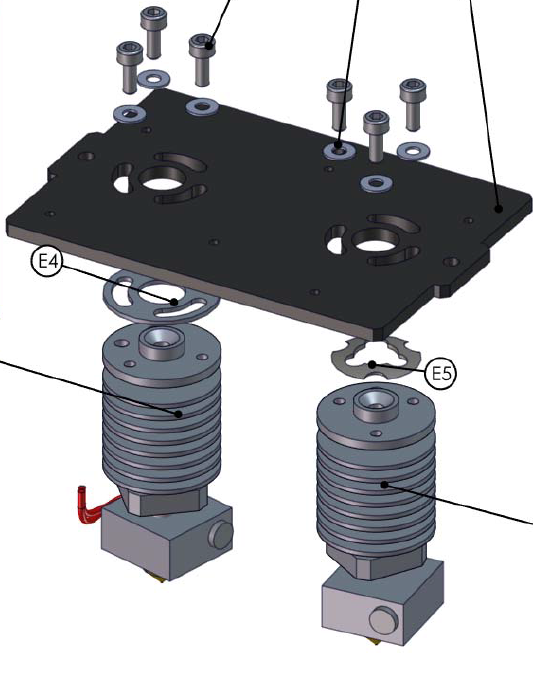
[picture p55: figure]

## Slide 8

1. CALIBRACIÓN EXTRUSOR 1

Esto servirá para tener el Extrusor 2 más alto que el Extrusor 1 y poder calibrar el 1 sin dañar el 2. Nos debería quedar algo así:

Extrusor 2

Extrusor 1

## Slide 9

1. CALIBRACIÓN EXTRUSOR 1

A continuación calibraremos el Extrusor 1 de la misma manera que se calibra la BCN3D+ con un solo extrusor. En las siguientes diapositivas se presenta un recordatorio de esta calibración.

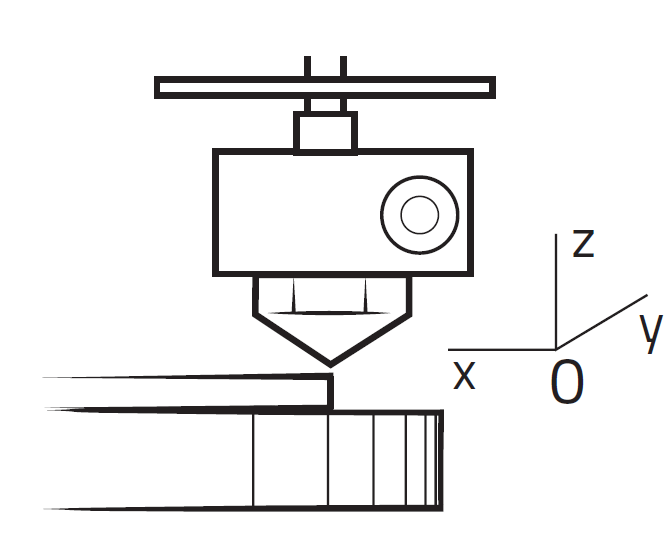
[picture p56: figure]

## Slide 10

1. CALIBRACIÓN EXTRUSOR 1

Recordatorio de cómo calibrar un solo extrusor (1/2):
1. Hacer Autohome (Prepare/Autohome) para que la máquina mueva los ejes a la posición inicial. La primera vez se debe ir con cuidado pues el nozzle puede colisionar con la base. Si se prevé que esto va a suceder, pulsar manualmente el final de carrera del eje Z.
2. Ajustar el tornillo que acciona el final de carrera, para que el nozzle esté a punto de tocar el cristal al hacer Autohome.

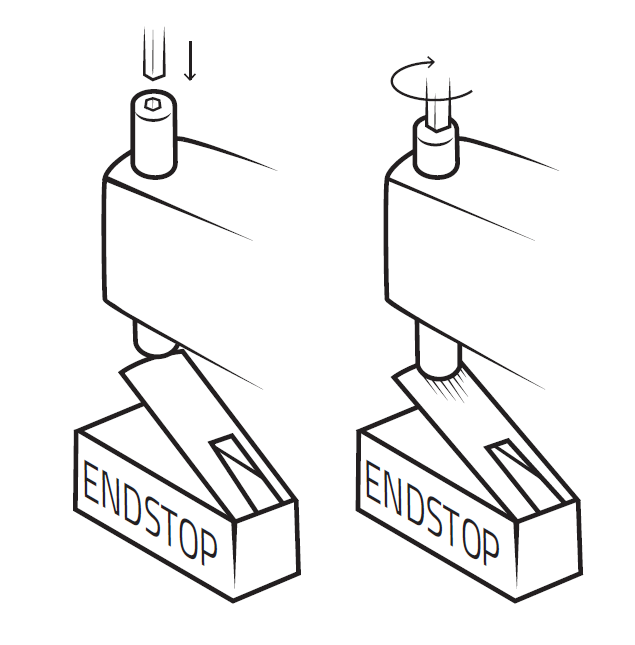
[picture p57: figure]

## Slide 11

1. CALIBRACIÓN EXTRUSOR 1

Recordatorio de cómo calibrar un solo extrusor (2/2):
3. Apretar/aflojar los tres tornillos negros que sujetan la base para nivelarla. La distancia entre la boquilla y el vidrio de la base calefactada tiene que ser de 0,2 mm. (Usar un papel doblado para comprobar este margen).
4. Mover el extrusor con la mano hacia el extremo izquierdo (si ofrece resistencia desactivar los motores en Prepare/ DisableSteppers). Nivelar la base con el papel doblado de la misma forma.
5. Mover la base hacia delante para hacer lo mismo en la parte trasera de la base.
6. Repetir este proceso hasta que la base esté nivelada en los cuatro extremos.

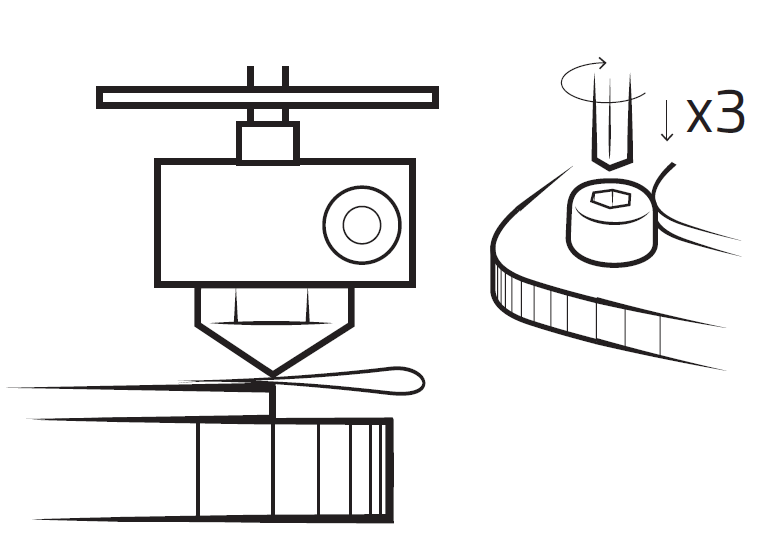
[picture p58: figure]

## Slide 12

2. CALIBRACIÓN EXTRUSOR 2

Una vez ya este calibrado el primer extrusor, se deberán aflojar los 3 tornillos del segundo extrusor para regular su altura.
Se deberán ir aflojando a la vez que se va comprobando mediante un papel doblado que el segundo extrusor roza de igual manera con el papel que el primero.

Arandela elástica

Ext 1

Ext 2

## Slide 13

2. CALIBRACIÓN EXTRUSOR 2

De esta manera se habrá logrado ajustar el Z offset y por tanto habrá la misma distancia entre el cristal y ambas boquillas.

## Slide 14

3. ACABAR EL MONTAJE

Con la ayuda del manual de montaje se seguirá montado el doble extrusor.


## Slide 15

4. ENCONTRAR XY OFFSET

Para proceder a obtener los valores de la distancia relativa entre boquillas (XY offset) serán necesarios 2 archivos, se podrán descargar en nuestra sección de descargas en la web o en la carpeta de calibración de la SD.
Abrir el Slic3r y cargar la configuración Dual_PLA_Slic3r.ini y la pieza Calib.amf.
Al cargar una configuración con múltiples extrusores aparece un warning. Eso se debe a que Slic3r solo carga la configuración del Filament Settings para el primer extrusor.
Por ello, conviene crear subconfiguraciones para cada tipo de plástico que se vaya a usar. Clicamos a aceptar y procedemos a cargar la configuraciones del segundo extrusor:
1. Ir a Filament Settings.
2. Hacer las modificaciones pertinentes de los parámetros para el plástico del segundo extrusor.

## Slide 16

4. ENCONTRAR XY OFFSET

3. Clicar el icono del disquete (save current filament settings). Guardar con el nombre deseado.


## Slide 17

4. ENCONTRAR XY OFFSET

4. En la pestaña Plater, al submenú de la derecha Filament, escoger la subconfiguración creada para cada uno de los extrusores.


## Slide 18

4. ENCONTRAR XY OFFSET

5. En función del resultado de la impresión, ajustar offset del extrusor 2: Printer Settings > Extruder 2 > Extruder Offset. En general el error máximo a corregir será de 1mm. A continuación se describe el sentido del ajuste mediante algunos ejemplos para arreglar la desalineación:


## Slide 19

4. ENCONTRAR XY OFFSET

6. Exportar la configuración con los valores del offset retocados: File > Export Config. Exportar G-Code y volver a imprimir la pieza.
7. Volver al paso 5 hasta conseguir el resultado óptimo. Ser riguroso con el resultado. El aspecto de las piezas futuras dependerá de una correcta calibración.


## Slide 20

4. ENCONTRAR XY OFFSET

En el caso de querer configurar el XY offset con el sofware CURA primero se deberá configurar la máquina BCN3D+ Dual extruder en Cura (ver Manual de impresión con Cura). A continuación se deberá cargar el archivo de calibración .amf y seguir los mismos pasos que en el Slic3r para encontrar la distancia de offset correcta.
En machine → machine settings se puede ir modificando el offset de la máquina.


## Esperamos que hayáis disfrutado de la experiencia! No olvidéis seguirnos en Twitter, Facebook y Google+


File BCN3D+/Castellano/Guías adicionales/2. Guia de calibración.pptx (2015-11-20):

## Guía de calibración Qué, cómo y porqué

Equipo RepRapBCN

## ¿Por qué?

- Calibración:
- Las máquinas de impresión 3D necesitan ser calibradas por varios motivos:
- Evitar posibles colisiones entre boquilla extrusora y base.
- Para imprimir con una buena primera capa y no tener problemas de despegue o warp.
- El simple funcionamiento de la máquina hace que se descalibre
- En el momento de retirar las piezas pueden producirse desajustes
- No calibrar puede provocar:
- Obtener fabricaciones defectuosas o poco precisas
- La rotura de alguno de los componentes (especialmente, boquilla o base de cristal)

Dudas?

## ¿Qué?

Para tener una máquina bien calibrada hay que conseguir lo siguiente:
- Paralelismo entre el plano de la base y el plano de movimiento del carro extrusor.
Implica que la distancia entre la boquilla y la plataforma debe ser la misma en todo el movimiento X y en todo el movimiento Y.
- Distancia adecuada entre la boquilla y la plataforma en la primera capa.
- Para que la máquina empiece a imprimir correctamente se debe conseguir, aproximadamente, una distancia de entre 1 décima y 2 décimas de milímetro entre la boquilla y la plataforma. Esto corresponde al grueso el de una hoja de papel doblada.

Dudas?

## ¿Cómo?

- Previo

- Comprobar que TODOS los finales de carrera están correctamente ajustados y que no hay impedimentos en el movimiento completo de los ejes X ,Y, Z:
  - Ajustar el final de carrera Z suficientemente lejos para que la boquilla no toque la placa de ninguna de las maneras
  - Tener cuidado con el cableado para que el movimiento de la base no desconecte nada
- Hacer Prepare > autohome y ver que pasa.
  - Vigilar el movimiento y comprobar que toque bien los finales de carrera
  - Estar preparado para parar la máquina si fuera necesario. (Botón rojo)

Dudas?

## ¿Cómo?

- Planitud de la plataforma

- Usando el útil de calibración, garantizar que los tres puntos de calibración están a la misma altura.
- Igualar esta distancia con los tornillos de ajuste si fuera necesario

Dudas?

## ¿Cómo?

Ajuste de la altura del eje Z

1. Colocar el extrusor a 1 cm del final de carrera del eje X
2. Ajustar gradualmente la distancia en el tornillo de calibración del eje Z hasta que la boquilla quede a 0,1mm de distancia.
  - Con un papel doblado, comprobar que este pasa entre la boquilla y la plataforma con cierta resistencia
3. Mover manualmente el extrusor a lo largo del eje X. Si se produce variación de la altura corregir la barra del lado donde NO ESTÁ el final de carrera Z.
  - Puede ser necesario reajustar la regulación del final de carrera Z.
4. Comprobar moviendo eje Y que la distancia se mantiene en dicho eje.

Dudas?

## Resultado

- La máquina debería estar calibrada. Para acabar de comprobarlo:
- Repetir la comprobación del papel pero esta vez a lo largo del eje Y.
- Comprobar la distancia en los cuatro extremos de la plancha.
- Es hasta cierto punto normal que no quede absolutamente igual en todas las puntas.
- Como la mayoría de las piezas empiezan en el centro, ese es el punto principal a comprobar.

Dudas?

## ¿Y si no puedo?

- Si al comprobar los puntos extremos quedan distancias muy dispares después de haber realizado los pasos anteriores:
- Volver a repetir el proceso desde “Planitud de la plataforma”
- En caso de no lograr calibrar correctamente:
  - Comprobar con un nivel que el eje Y esta igual de inclinado en sus dos extremos.
    - La inclinación debe ser igual pero no tiene porque ser plano ya que depende de la superficie en que se monte la máquina.
    - La burbuja debe estar en la misma posición teniendo la misma distancia en los cuatro tornillos de la plataforma como se ha hecho anteriormente.
  - Si hay error habrá que ajustar los soportes de las barras e intentar obtener una orientación estable.
- En general esto último no suele pasar, así que ante la duda, probar de repetir el proceso antes de llevar a cabo este ajuste.

Dudas?

## Esperamos que hayais disfrutado de la experiencia! No olvidéis seguirnos en Twitter y Facebook Para cualquier duda visita nuestro foro (http://www.reprapbcn.com/es/forum)!

- Equipo RepRapBCN

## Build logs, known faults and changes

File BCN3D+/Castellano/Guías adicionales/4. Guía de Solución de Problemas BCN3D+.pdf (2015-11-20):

# GUÍA DE SOLUCIÓN DE PROBLEMAS

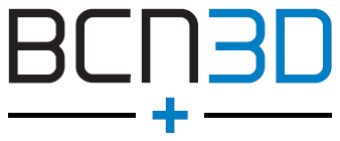
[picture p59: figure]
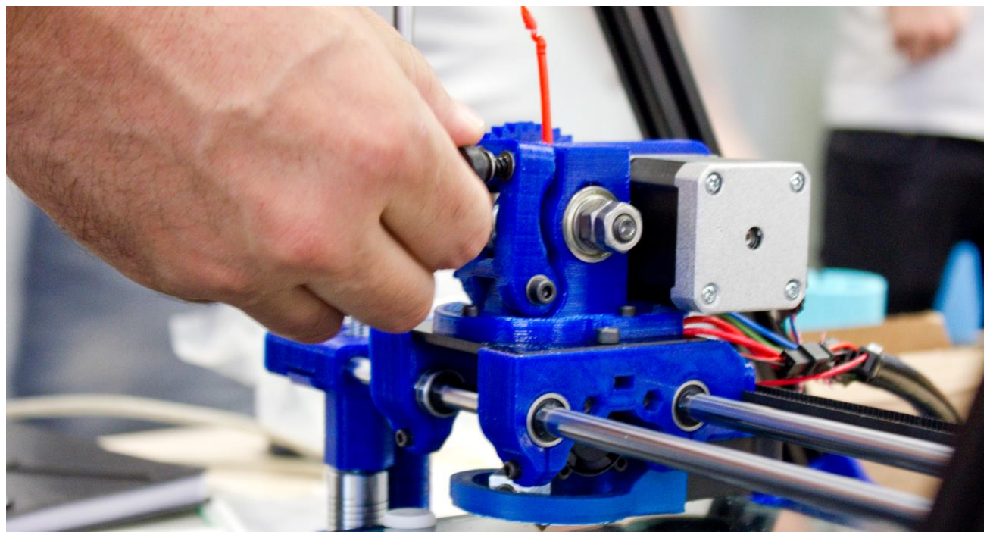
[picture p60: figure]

# INTRODUCCIÓN

En este manual se explican los procedimientos de solución de problemas que pueden llegar a presentarse durante la utilización de la BCN3D+, los cuales se pueden clasificar en dos categorías:

1. Solución de problemas de calibración, mantenimiento y operación de la máquina
2. Solución de problemas en la calidad de impresión de las piezas

Esta guía tiene la intención de ser usada como referencia para el usuario en la resolución de los problemas más frecuentes. En caso de presentarse algún problema al cual no se haga referencia, se recomienda consultar con el Servicio de Asistencia Técnica de RepRap BCN al siguiente correo: sat@reprabcn.com

El contenido de este manual está sujeto a cambios sin previo aviso.

La BCN3D+ cuenta con un repositorio de documentación disponible en la web (http://reprapbcn.github.io/) donde se puede acceder a toda la información relacionada con su funcionamiento (configuraciones de impresión, manuales, archivos STL, firmwares, etc…).

# CONTENIDO

### Solución de problemas de calibración, mantenimiento y operación de la máquina

En este apartado se muestran los procedimientos de solución de problemas más frecuentes relacionados con calibración, verificación y ajustes de componentes mecánicos y electrónicos de la máquina. Para la resolución de problemas relacionados con la calidad de las piezas referirse al siguiente apartado.

### Calibración de la superficie de impresión

Para un correcto funcionamiento de la impresora, es clave que el plano de movimiento de la boquilla sea perfectamente paralelo a la superficie de la cama calefactora.

Y para conseguirlo, es necesario calibrar la orientación de la cama mediante los 3 tornillos de nivelación.

Con una base mal calibrada NO SE PUEDE IMPRIMIR, y se corre el riesgo que la boquilla (nozzle) colisione contra el cristal. También puede generar que la primera capa de la impresión no se adhiera. Para calibrarla correctamente se deben seguir los siguientes pasos:

1. Hacer Autohome (Prepare/Autohome) para que la máquina mueva los ejes a la posición inicial. La primera vez se debe ir con cuidado pues el nozzle puede colisionar con la base. Si se prevé que esto va a suceder, pulsar manualmente el final de carrera del eje Z.
2. Ajustar el tornillo que acciona el final de carrera del eje Z, buscando que el nozzle quede a una distancia de 0,2 mm del cristal (equivalente a una hoja de papel doblada) al hacer Autohome.
3. Desplazar los ejes a lo largo y ancho (X,Y) de la superficie de impresión validando que la distancia se mantiene constante en toda la superficie. Apretar/aflojar los tres tornillos con los muelles que sujetan la base para nivelarla.
4. Repetir este proceso hasta que la base esté nivelada en los cuatro extremos.

5.

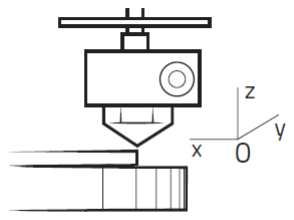
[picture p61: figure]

Figura 1 Calibración de la distancia entre boquilla-cristal

### Desplazamiento deficiente de los ejes

Los ejes de la BCN3D+ deben poder moverse sin obstrucciones mecánicas y deben estar correctamente calibrados. Si no hay obstrucciones mecánicas al movimiento de los ejes y los motores siguen perdiendo pasos o se desplazan de manera incorrecta (se frenan o se desplazan a trompicones), lo más probable es que los controladores electrónicos de los motores no estén bien ajustados (ver: Ajuste de los controladores de los motores paso a paso).

La BCN3D+ se comercializa montada y calibrada, pero es posible que con el tiempo requiera un recalibrado de sus ejes.

El proceso es sencillo si se siguen los pasos siguientes:

- Calibración eje X
a) Con el útil de calibración, medir la altura de las barras del eje X (en cada extremo), desde las chapas de aluminio de la base.
b) Ajustar la altura en ambos extremos del eje para garantizar su horizontalidad. Para ello girar manualmente el acople de las varillas roscadas.

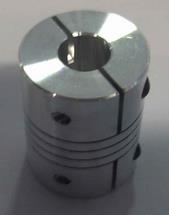
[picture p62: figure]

Figura 2 Acople entre las varillas roscadas y los ejes de los motores
- Calibración eje Y

El eje Y debe ser capaz de desplazarse en todo su recorrido manualmente y sin excesivo roce. Para esto los rieles en los cuales se desplaza la superficie deben estar paralelos.

- Calibración eje Z

Con el fin de garantizar la perpendicularidad del eje Z con la base, se debe realizar un proceso iterativo que consiste en los siguientes pasos:

a) Colocar el eje Z en una posición elevada (180 mm aproximadamente).
b) Aflojar los tornillos de la base de las guías lineales (barras lisas) del eje Z. Con ello se consigue un margen de movimiento que nos permitirá posicionarlos correctamente.
c) Usar el útil de calibración a modo de escuadra. Apoyar su lado corto sobre las chapas de la base de la impresora, y el lado más largo en contacto con las guías verticales del eje Z.

d) Orientar el útil de modo que permita hacer 2 mediciones a 90º y realizar esta operación en ambas guías Z.
e) Durante las mediciones, ir ajustando la perpendicularidad de las guías con el útil, e ir apretando los tornillos de la base para fijar su posición. Como se ha comentado, éste es un proceso iterativo, de modo que una vez se ha aplicado en ambas guías, se debe repetir y corregir posibles desajustes.

Después de haber finalizada la calibración, se deben lubricar los ejes X,Z (ver: lubricación de los ejes)

### La impresora no extruye material

El primer paso para resolver este problema es verificar que la temperatura del extrusor es superior a los 150ºC. El extrusor en frío no se mueve.

Es importante verificar que el extrusor no está atascado: con el extrusor caliente (a 220ºC para PLA o 260º para ABS) y con los tornillos que aprietan el filamento completamente aflojados (“extruder idler”) tratar de empujar el filamento a través del extrusor haciendo presión hacia abajo con unos alicates. Si el material no se extruye a través de la boquilla o cuesta un gran esfuerzo significa que el extrusor está atascado (ver: Mantenimiento del hot end).

En caso de no estar atascado se debe comprobar el correcto funcionamiento del motor del extrusor. Nuevamente, con el extrusor en caliente y los tornillos del “extruder idler” aflojados mover el motor del extrusor a través de la opción del menú de la pantalla: prepare-move axis-move 1mm-extruder. Si no se mueve, comprobar conexiones y ajustar el pololu del motor (Ver: Ajuste de los controladores de los motores paso a paso). También verificar que no hay obstrucciones en el giro de los engranajes, los cuales deben girar suavemente con la mano.

Si el motor se mueve y el extrusor no está atascado: apretar o aflojar los tornillos que aprietan el hilo. Comprobar que el hilo no este enredado en algún sitio y que el tornillo grafilado que empuja el filamento no esté desgastado.

### La impresora extruye material pero de forma deficiente

Al inicio de la impresión casi siempre le costará un poco extruir. Si pasado un rato el hilo sale de forma intermitente o a borbotones entonces hay que determinar la causa de este fallo.

Soluciones y comprobaciones:

- Comprobar que la temperatura es la adecuada para el material que se intenta imprimir (ver: Descarga de las configuraciones para Slic3r).
- Verificar que el tornillo grafilado que arrastra el filamento no presenta desgaste en los dientes.
- Dejar que fluya un rato, podría tener impurezas adentro.
- Ajustar los tornillos que aprietan el hilo.
- Limpiar la boquilla con acetona (o un producto similar)
- Comprobar que el hilo no esté enredado en algún sitio.

### Ajuste de los controladores de los motores paso a paso (Pololus)

El ajuste de los pololus puede realizarse con dos procedimientos:

- Usando el tester (voltímetro)
- Sin el uso del tester, en un proceso iterativo.

El procedimiento con el tester es preciso pero implica un riesgo de generar un cortocircuito que dañe los componentes electrónicos de la máquina (debe ser realizado con mucha precaución). El procedimiento sin el tester es iterativo y puede requerir un tiempo más prolongado.

Usando el tester: lo que se busca es verificar la tensión existente en el pololu a ajustar con un multímetro (tester). El selector del multímetro debe ser colocado en la posición de la figura 1. En la figura 2 y 3 se muestran donde se tienen que colocar las puntas del tester en el pololu. La flecha roja señala el tornillo (potenciómetro) y la negra el pin de la esquina con base cuadrada (ground). La tensión se aumenta dando vueltas al potenciómetro en sentido horario y se disminuye en sentido antihorario. Se debe hacer con mucha precaución, ya que al tocar otros componentes o pines se podría producir un cortocircuito.

Los valores de tensión a la cual se deben ajustar:
- 0,45V en los pololus de los ejes
- 0,55V en el del extrusor

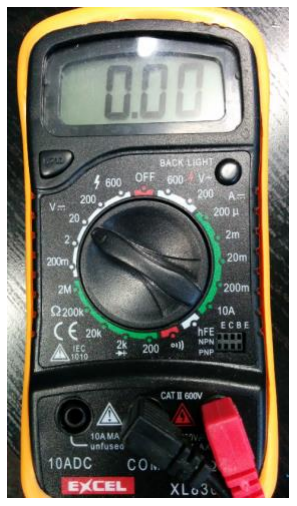
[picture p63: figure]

Figura 1 Posición del selector del tester para ajuste de pololus

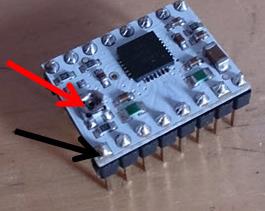
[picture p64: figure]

Figura 2 Ubicación de las puntas del tester para la calibración de pololu blanco

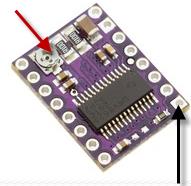
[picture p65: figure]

Figura 3 Ubicación de las puntas del tester para la calibración de pololu lila

Sin tester: el pololu tiene una pequeña rueda con un plano y una cruz. Éste es el potenciómetro que nos permite controlar el corriente que llega al motor. Girando esta rueda en sentido horario, se logra transmitir una mayor potencia al motor, y en sentido antihorario se reduce. Con la impresora preparada para funcionar, se mueven los ejes a través del menú de la pantalla: move axis. A partir de aquí, se actúa según lo que se observa. Si los motores no se mueven o no se mueven lo suficiente, les falta potencia. Para aumentar la potencia, se apaga la impresora y se gira el potenciómetro del eje observado no más de 5 minutos de reloj en sentido horario. Se vuelve a encender y se observa el desplazamiento del eje con la opción: move axis. Si el eje se mueve bruscamente, haciendo demasiado ruido o al poner la mano en el motor sentimos un pulso, los motores reciben demasiada corriente. Se debe apaga r la impresora y girar en sentido anti horario no más de 5 minutos el potenciómetro del pololu en cuestión. Tras eso, se vuelve a observar el movimiento de los ejes. Finalmente, si todo parece que se mueve correctamente, se realiza una última prueba. Con la mano, se ofrece cierta resistencia al movimiento del eje que se está observando. Normalmente esto se hace en el eje X e Y. Con esto, se tiene la seguridad que la potencia aunque no sea baja para el movimiento de los ejes, es suficiente para impresiones rápidas. Se debe observar la pérdida de pasos del eje al ofrecer dicha resistencia. Si ocurre, se actúa como en el supuesto de falta de potencia, pero ajustando el potenciómetro lo más finamente posible 1-2 minutos de reloj en sentido horario. Volver a encender y observar. Es un proceso iterativo, pero es necesario hacerlo de este modo debido a la gran variabilidad que hay entre las máquinas de todos los usuarios.

### No calienta la base / el extrusor

Si la base o el extrusor no alcanzan la temperatura deseada (la base, que es lo que más tarda, debería tardar menos de media hora en estabilizarse) realizar las siguientes comprobaciones:

En el extrusor:

- Comprobar el conexionado y que ningún cable de la boquilla este suelto o quemado.

En la base:

- Tener en cuenta que la temperatura máxima que puede alcanzar la base es de unos 85º (dependiendo de la temperatura ambiente y de las corrientes de aire)
- Comprobar el conexionado.
- Comprobar la integridad de las resistencias.

### La pantalla no se enciende

En este caso se deben realizar las siguientes comprobaciones:

- Revisar la salida de voltaje de la fuente de alimentación a 12 VCD (con un multímetro). El voltaje se puede ajustar con un tornillo situado al lado de las conexiones de los cables.
- Verificar el estado de los cables de la pantalla que provienen de la RAMPS, asegurarse que están bien conectados (deben cruzarse, no van paralelos).
- Cargar de nuevo el firmware desde un PC. Si el firmware está mal cargado la pantalla aparecerá en blanco (ver Firmware)
- Conectar la impresora directamente al PC con el cable de puerto USB y validar si la pantalla se enciende.

### La pantalla se ve deficiente

En la LCD se pueden dar los siguientes errores:

- La pantalla esta iluminada pero no aparece ningún carácter en ella.
- Aparecen caracteres extraños en la pantalla.
- La pantalla está excesivamente iluminada (se ven cuadros blancos en vez de los caracteres)

Para solucionarlos:

- Si la maquina está imprimiendo correctamente se puede esperar a que acabe, después reiniciarla.
- Si el problema persiste, comprobar el cableado de la LCD.
- Ajustar el potenciómetro que se encuentra en el reverso de la pantalla hasta que se vea correctamente.

### La impresora no lee correctamente la tarjeta SD

Este problema puede deberse a que haya algo de suciedad en la ranura de la SD o que el firmware haya leído incorrectamente la información.

Para solucionarlo basta con limpiar el alojamiento de la tarjeta SD y reiniciar la impresora.

Si el problema persiste, comprobar que los cables que unen la pantalla LCD con el resto de la electrónica no sean muy largos. Si miden más de 40-45 cm. la impedancia que generan hace que no se lean bien los datos.

### Aparece el error MINTEMP en la pantalla

El error MINTEMP es debido a una mala conexión o desconexión del termistor del extrusor o de la cama caliente. En este caso, se debe tratar de asegurar una correcta conexión con el manual de cableado.

### Aparece el error MAXTEMP en la pantalla

El error MAXTEMP es debido a un cortocircuito en el termistor del extrusor o de la cama caliente. En este caso, se debe reemplazar el termistor.

### Lubricación de los ejes

Se recomienda lubricar las varillas d elos ejes X,Z cada cierto tiempo, en especial cuando los ejes no se mueven con facilidad o hacen más ruido de lo normal. Para ello se puede usar cualquier tipo de aceite lubricante anticorrosivo para bricolaje. Colocar unas gotas en las varillas roscadas y lisas. Posteriormente, mover los ejes para que el mismo mecanismo las reparta por toda su extensión. Las guías lineales del eje Y no requieren lubricación.

### Almacenamiento del filamento

Las bobinas de filamento se deben guardar en un lugar fresco y seco. El calor y la humedad afectan bastante a este tipo de plásticos. Si una bobina no se va a usar durante un largo período de tiempo, guardarla en una bolsa de plástico sellada.

Debe asegurarse que el plástico esté bien enrollado. Una bobina con el plástico suelto puede provocar tirones que afectan a la impresión y los componentes de la máquina.

### Limpieza de la base de impresión

Después de varias impresiones, el cristal de cama caliente se ensucia, y se acumulan capas de laca, polvo y restos de plástico.
Para limpiar el cristal se debe retirar de la impresora. Los restos de laca y polvo se quitan fácilmente poniendo el cristal debajo del agua con un poco de jabón. Si hay restos de plástico enganchados, se pueden retirar con un cúter con cuidado de no dañar el cristal. También se puede usar acetona, ya que disuelve el plástico (sobretodo ABS).

### Atascamiento del hotend

El Hotend es un componente que comprende las siguientes piezas: disipador de calor, boquilla, heat break (barrera térmica) y bloque calefactor. En ocasiones, es posible que se

atasque.

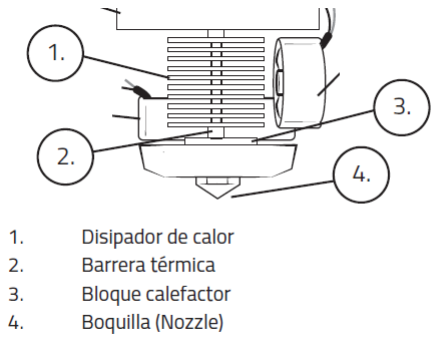
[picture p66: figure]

Figura 4 Hot End BCN3D+
Si el extrusor se ha obstruido, se deben realizar las siguientes comprobaciones.

En primer lugar, se debe verificar visualmente que la boquilla no se ha deformado. Esto puede ocurrir si la boquilla golpea el cristal durante una impresión. En caso de notar deformación, debe ser reemplazada la boquilla.

Verificar el funcionamiento del ventilador del disipador. Si el ventilador dejase de funcionar podría ocasionar la subida de material fundido y resultar en un atascamiento del extrusor. En este caso habría que verificar el cableado y que no esté invertido con el ventilador de capa o reemplazar en caso de fallo.

Si el hilo contiene impurezas podría atascarse el extrusor, por lo tanto el hilo debe estar limpio y debe provenir de un proveedor confiable.

Si se requiere desmontar el hotend para cambiar la boquilla o alguna otra de sus partes se puede realizar fácilmente siguiendo estos pasos:

- Desmontaje del Hotend
1. Extraer el filamento restante
2. Enfriar hotend durante unos 15 minutos con la opción Prepare > Cooldown.
3. Hacer Auto home y subir el eje Z hasta +150.00 mm
4. Apagar la alimentación de la máquina
5. Sacar los dos tornillos M3 del ventilador de capa
6. Desconectar el conector del ventilador y sacar la sujeción del cooler fan del Heat sink.

7. Desenroscar el conjunto “Barrera térmica+Bloque+Boquilla” del Disispador introduciendo una llave en el bloque (vigilar que los cables no se enreden o se descrimpen). Con este conjunto extraído, desenroscar la boquilla del bloque, vigilando no romper los cables. [View 5]

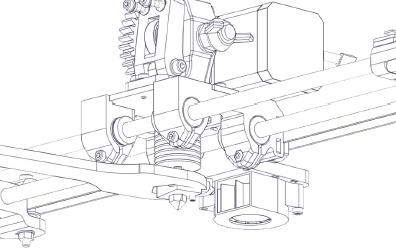
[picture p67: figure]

Figura 5 Desmontaje Hotend
8. Desenroscar la barrera térmica del bloque.
9. Comprobar que todos los componentes estén limpios, si no, limpiarlos cómo se describe más adelante.

Para limpiar restos de plástico de ABS o PLA se debe sumergir el componente en acetona y dejar varias horas en remojo. Posteriormente, eliminar los restos con un trozo de alambre que no arañe las partes.

- Montaje del Hotend
1. Partimos del bloque (con resistencia y termistor instalados), boquilla y barrera térmica por separado.
2. Atornillar la boquilla al bloque con la mano hasta que se tope con el bloque.
3. Una vez atornillado, aflojar un cuarto de vuelta.
4. Atornillar con la mano la barrera térmica al bloque hasta que tope con la boquilla.
5. Apretar fuerte la boquilla aguantando el bloque con otra llave.
6. Atornillar el conjunto a mano al disipador.
7. Apretar suavemente la barrera térmica en el disipador de la máquina.
8. Conectar los cables del hotend.
9. Calentar el extrusor a 220ºC.
10. Volver a apretar, ahora en caliente, la boquilla contra el bloque mediante la llave boquilla y la llave bloque.

### Actualización de Firmware

El firmware es el software necesario para controlar un hardware. Es decir, es el programa interno que controla la BCN3D+, y permite que desempeñe sus funciones normalmente. La BCN3D+ se entrega ya instalada con la última versión del firmware publicada en la web.

Será necesario actualizar el firmware siempre que cambiemos alguna funcionalidad de nuestra máquina que implique un cambio en su sistema de control. Por ejemplo, un nuevo cabezal extrusor, dual extruder, paste extruder, etc…También es necesario si se cambia cualquier componente de nuestra máquina como tamaño de poleas, finales de carrera, termistores, longitud de ejes, velocidades o aceleraciones de impresión…

Finalmente, se puede cambiar el firmware al recibir una actualización de RepRapBCN. En estos casos se anunciará su publicación vía página web y redes sociales, y sus mejoras y novedades respecto la versión anterior. Para actualizar el firmware se debe proceder de la siguiente forma:

El primer paso consiste en instalar el IDE de Arduino en un ordenador. Este es el programa que nos permitirá interactuar con la tarjeta Arduino de la BCN3D+.

Descargar el paquete de software ARDUINO de la web http://www.reprapbcn.com o abrirlo desde el USB subministrado. Manual

Una vez instalado, conectar la BCN3D+ al ordenador mediante un cable usb. De esta manera se establece la conexión con el Arduino.

La primera vez que se conecta una placa a un ordenador hace falta instalar los drivers del componente. Si el ordenador no instala los drivers automaticamente al conectar la placa, seguir los pasos explicados en:

http://arduino.cc/en/guide/windows#toc3

Abrir la aplicación Arduino

Desde el menu Archivo>Abrir, seleccionarla versión de firmware guardada (descargada anteriormente).

El archivo que se debe abrir tiene extensión*.ino, y se encuentran en una carpeta con el mismo nombre, mezclado con todos los subprogramas del firmware.

En este momento se pueden modificar los parámetros deseados si es necesario.

Seleccionar el modelo de tarjeta Arduino y el puerto desde Herramientas>Tarjeta>Arduino Mega 2560 y Herramientas>Puerto Serial>COM X

La tarjeta con la que opera la BCN3D+ es una Arduino Mega 2560.

El puerto se refiere al conector dónde tenemos conectada la placa en el ordenador (Puerto COM). Podemos consultarlo en el sistema operativo (Windows) desde Inicio>Equipo>Botón derecho>Propiedades>Administrador de Dispositivos> Puertos COM y LPT.32. Seleccionar el botón Cargar.

Empieza la carga, primero con la compilación del programa para detectar errores, y a continuación con la propia carga en la memoria de la placa.

Si el proceso termina correctamente se mostrará el mensaje “Carga terminada”, y la impresora estará lista para utilizar.

### Solución de problemas en la calidad de impresión de las piezas

En este apartado se va a hacer una lista de los problemas de calidad de impresión más comunes, y la manera de corregirlos o minimizarlos.

### Descarga de las configuraciones para Slic3r

El equipo de I+D de RepRap BCN ha desarrollado configuraciones especialmente diseñadas y probadas para la BCN3D+ en distintos materiales que pueden ser cargadas en el software de utilización libre Slic3r y descargadas del nuevo repositorio de documentación en el siguiente link:

http://www.reprapbcn.com/es/content/nuevo-repositorio-de-documentaci%C3%B3n-cad-y-configuraciones

### Separación de la pieza de la cama calefactada (WARPING)

A veces las piezas no se adhieren bien al cristal del hotbed durante la impresión. Esto sucede sobre todo imprimiendo con ABS, un material con mucha contracción térmica. En este caso probar las siguientes soluciones:

1. Limpiar bien el cristal para evitar que el polvo u otras substancias interfieran entre la base y la pieza.
2. Impregnar la superficie de cristal con una capa de laca
3. Subir la temperatura de la base cinco grados centígrados.
4. Calibrar la base de impresión como se explica en el apartado 11 Mantenimiento.
5. Imprimir la primera capa con el hotend más cerca de la base. Para ello, aflojar los tres tornillos de la base un octavo de vuelta, o aflojar el tornillo que acciona del final de carrera del eje Z un quinto de vuelta. Las dos acciones provocarán que la base y el hotend estén 0,1mm más cerca, y la primera capa se adherirá mejor.
6. | Hacer | que | la | primera | capa | eche | más | material | (desde | Slic3r,
PrintSettings/Advanced/FirstLayer).

### La primera capa no extruye material en toda la geometría

Puede suceder que la primera capa no se adhiera correctamente al cristal, o no deje un flujo constante de hilo plástico (únicamente una línea de gotas) en toda la figura.

El problema en este caso es que la máquina no está calibrada correctamente; el extrusor está demasiado lejos de la base. Revisar el calibrado (ver: Calibración de la superficie de impresión)

Si la primera capa presenta uno de los síntomas anteriores solo en una zona de la figura. La causa es que la impresora no está calibrada correctamente. El eje X y la base no son paralelos y esto provoca que el extrusor se aleje o se acerque demasiado a la base en algunos, centrándose en la orientación del plano de la base de impresión.

### Aparecen grietas en mitad de la pieza

Esto sucede porque la parte de la pieza más cercana al extrusor está más caliente que las capas inferiores. Si a esto se le suma que el plástico del perímetro se refrigera antes que la parte interior, se generan unas contracciones internas que pueden llegar a separar las capas de la pieza.

Para evitar estas grietas se debe subir 5 grados la temperatura de extrusión, de manera que las capas se adhieran con más fuerza.

### Una capa está desplazada respecto de la anterior

Esto se produce cuando un motor de los ejes X o Y pierde pasos (es decir, el movimiento del eje no se llega a ejecutar en la plataforma o carro del extrusor).

Para resolver esto lo primero que hay que hacer es comprobar que no haya nada que impida el movimiento de los componentes (cables enredados, piezas que se puedan tocar, etc.), Ver si las correas están tensas, las poleas no deslizan en el eje d elos motores y la lubricación de las guías.

Es posible que haya que ajustar los drivers de los motores (Pololu) a la potencia correcta (ver: Ajuste de controladores de los motores paso a paso).

También podría estar ocasionado por falta de apriete de los 2 tornillos de la pieza de PLA que une la correa con la lámina inferior de la cama.

Como último recurso, puede ser necesaria la sustitución del motor o el cable de extensión que viene de la RAMPS. Utilizar el motor y el cable de otro eje para validar su funcionamiento.

### La pieza sale "chafada"

Este error es el mismo que el anterior pero cuando son los motores del eje Z los que pierden pasos. En este caso conviene comprobar el paralelismo de las barras roscadas y que ambos extremos del carro X estén a la misma altura. Es posible que se resuelva ajustando el driver de los motores a la potencia adecuada (ver: Ajuste de controladores de los motores paso a paso). Verificar cable y motor.

### Las capas no están bien pegadas entre si

Esto se nota cuando la pieza final no está bien cohesionada y, si existen, las paredes finas crujen y se rompen con facilidad.

Esto se produce porque la temperatura de trabajo del extrusor no es suficiente o porque el extrusor está ligeramente obturado y no saca suficiente material. Aumentar la temperatura de extrusión o limpiar extrusor para resolver este problema.

### Las esquinas no están bien definidas

En estos casos se dan, generalmente, dos errores:

- El primero es que queden rebabas en las esquinas producto del comienzo o final de la impresión del perímetro. Para arreglar esto conviene modificar el Retract y/o la temperatura del extrusor porque igual está demasiado caliente.

- El otro error típico es una mala geometría en las esquinas. Esto se debe a que la máquina fabrica los perímetros de las piezas demasiado rápido y cuando tiene que hacer el cambio de dirección, el extrusor vibra y no realiza correctamente el trazado. Para solucionar esto disminuir la velocidad de fabricación en los perímetros en el Slic3r.

### Se levanta una esquina

Esto se debe a la contracción de las piezas. Al trabajar a altas temperaturas (180 o 230ºC según que material) y, estando la maquina abierta al ambiente, el contraste entre ambas temperaturas provoca que la pieza se contraiga. Sin embargo, la capa que está pegada a la base no puede contraerse con el resto de la pieza por lo que tiende a doblarse hacia arriba. Para solucionar este problema se pueden hacer dos cosas:

1. Aumentar la temperatura de la base para que el contraste entre la primera capa y el ambiente sea menor.
2. Colocar material adicional en la primera capa modificando el parámetro “brim” (Slic3r), lo cual aumentará la superficie de contacto y evitará en parte que este efecto ocurra.

### Aparecen hilillos de plástico alrededor de la pieza

Esto sucede cuando el extrusor se desplaza de un punto a otro sin depositar material.

Para evitarlo, ajustar la opción retract desde Slic3r. Esta opción retira parte del hilo del motor del extrusor, de manera que se disminuye la presión del material en el interior del extrusor y se evita el goteo durante el desplazamiento de los ejes. Si se aumenta el retract, se disminuyen los residuos en forma de hilos.

También es posible que este problema aparezca cuando se trabaja con temperaturas del extrusor muy altas para el material.

### Material de apoyo

Al ir subiendo en altura, el material imprimido necesita tener un apoyo. Son muchas las piezas que contienen partes suspendidas en el aire (voladizos) o zonas con mucha inclinación, y el material depositado tiene tendencia a desprenderse hasta enfriarse.

Cuando esto ocurra, se recomienda investigar la creación de columnas de apoyo desde el software de impresión (Slic3r).

También se puede considerar la modificación de la BCN3D+ agregando el extrusor doble (http://www.reprapbcn.com/es/node/530), el cual permite imprimir piezas con material de soporte. El material de soporte puede ser removido con agua después de finalizar la impresión.

### Una capa aparece desplazada respecto a la inferior

Cuando en una pieza existe un desfase de posición entre una capa y las siguientes, lo más seguro es que uno de los motores haya perdido pasos. Primero se debe identificar cuál de los ejes se ve afectado, y después ajustar el pololu correspondiente a ese motor (ver: Ajuste de los controladores de los motores paso a paso).

También se debe verificar que no se hayan aflojado los tornillos de la pieza de PLA que une la correa con la superficie inferior de la superficie calefactada.

### Impresión de círculos y cilindros (histéresis y backlash)

Los problemas con la impresión de círculos se deben principalmente al problema de la histéresis. El efecto de la histéresis es puramente mecánico y derivado del backlash se lleva a cabo en los componentes usados en las BCN3D+. La plataforma tarda unos instantes en el momento en el cual debe cambiar la dirección de desplazamiento para proseguir con el dibujo de una figura, lo cual genera problemas de impresión. Éste efecto es lo que llamamos histéresis. El efecto se produce básicamente en el cambio de dirección del eje Y. El resultado de este fenómeno se puede apreciar sobretodo en la impresión de círculos, donde se produce un alargamiento de la forma justo en los puntos de cambio de eje.

Para resolver este problema se ha desarrollado un nuevo firmware, el cual se puede descargar de nuestra página (http://www.reprapbcn.com/es/content/firmware-release-bcn3d-v30-hysteresis-correction) y permite ‘forzar’ la corrección del eje y o x justo en el momento en que éste cambia de dirección. En el punto de cambio de dirección, se obliga a la plataforma de impresión a corregir su posición bajando o subiendo según en la dirección que se haya producido el cambio. De este modo se arregla el hecho que la plataforma no pueda cambiar de dirección rápidamente (histéresis) y, por lo tanto, desaparece el alargamiento citado anteriormente.

Una vez instalado el firmware, se puede acceder al menú Histéresis desde:

Menú principal > Control > Motion > Hysteresis33

Dentro del menú de histéresis encontramos las opciones:

- Círculos: Nos configura unos valores de corrección estándar para realizar círculos
- Manual x: Permite fijar manualmente la corrección de la histéresis en el eje x
- Manual y: Permite fijar manualmente la corrección de la histéresis en el eje y
- Disable: Desactiva la corrección de la histéresis

Ésta actualización de firmware ya viene con un valor de corrección de histéresis preestablecido para que se puedan empezar a imprimir círculos sin problema.

### La pieza se suelta de la base

Este problema es causado por la contracción térmica de las piezas. Se puede resolver añadiendo laca, acercando el cabezal a la cama en la opción auto home (ver: Calibración de la superficie de impresión) o aumentando la temperatura de la primera capa. También se puede modificar el parámetro “brim” en el Slic3r para aumentar la superficie de contacto entre la primera capa y el cristal.

### Las piezas no salen "rectas"

La falta de perpendicularidad se ve cuando las piezas no salen completamente rectas, es decir, cuando una esquina teóricamente de 90º queda en otro ángulo. Para solucionar esto hay que comprobar la perpendicularidad en el eje X y en el eje Y.

### Las capas se notan excesivamente

Es considerado un problema de definición. La altura de capa es un parámetro que puede ser modificado en cualquier software de creación de g-codes (ej.: Slic3r). Al disminuir la altura de capa, se notarán menos pero se imprimirá más lento la pieza. Por otro lado, en el PLA las capas se notan más que en el ABS. Las piezas de ABS pueden ser tratadas con vapor de acetona para otorgarles un aspecto liso.

### El hilo de extrusión no sale en un diámetro constante

Esto se nota mucho cuando el infill es inconstante y es producido por varias razones. Los tornillos que aprietan el hilo en el extrusor están demasiado apretados o, todo lo contrario, demasiado flojos. En este caso ajustar los tornillos hasta que el flujo sea constante. Otra posibilidad es que la boquilla este sucia o deformada. En estos casos, la solución es limpiarla o reemplazarla (ver: Atascamiento del hotend).

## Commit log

2014-09-25 info updated in README.md
    A couple of pictures and some useful info
2014-10-24 Correcio 3DVIA 1.Structure
    Separar más les nuts pera facilitar el montatge
2015-11-20 Updated manuals
    [Calib.amf, bulbasaur.STL, star-vase.stl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]
